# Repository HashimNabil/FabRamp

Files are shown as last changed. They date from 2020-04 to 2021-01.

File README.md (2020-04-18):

# FabRamp

Fabramp is Ramp 1.4 fabable board! its based on Atmega2560 and comes with the following features:
- 6 PWM terminals with STP55NF06L transistors that can be used for multiple Extruders/hot bed/fans
- Extruder Fan terminal
- 2 Extruders terminals with built in Polulu drivers (one of them have terminals for external driver)
- 3 Thermometer terminals with filtering capacitors
- Terminals for 3 axis motors (X, Y and Z)
- Terminals for End stops for all Axis (2 per Axis)
- BLtouch Auto level sensor terminals
- ISP headers
- USB support
- 12V Power terminals with 20A diode as reverse voltage protection
- 5V input with 5A diode as reverse voltage protect

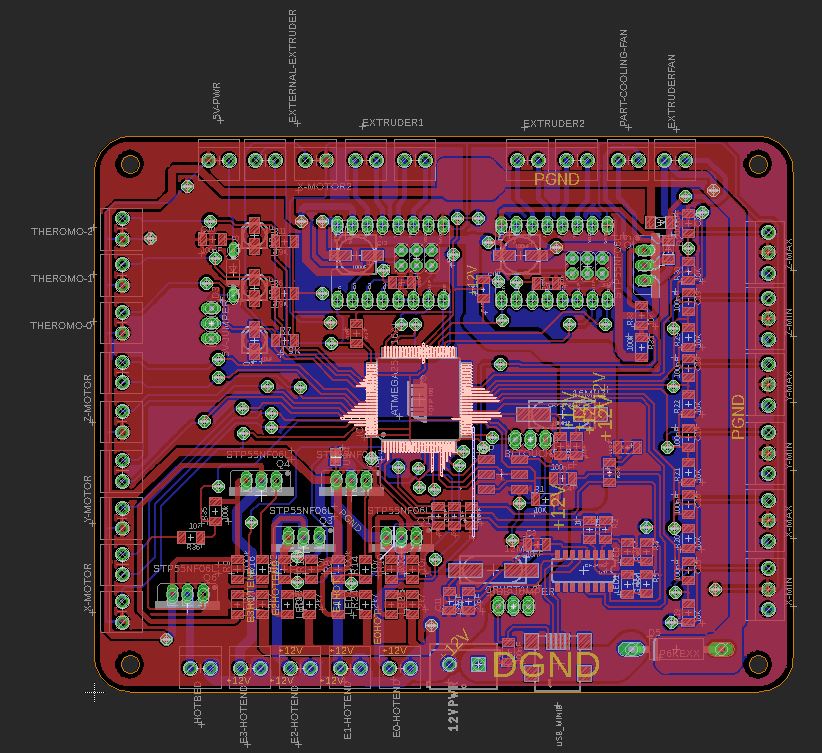
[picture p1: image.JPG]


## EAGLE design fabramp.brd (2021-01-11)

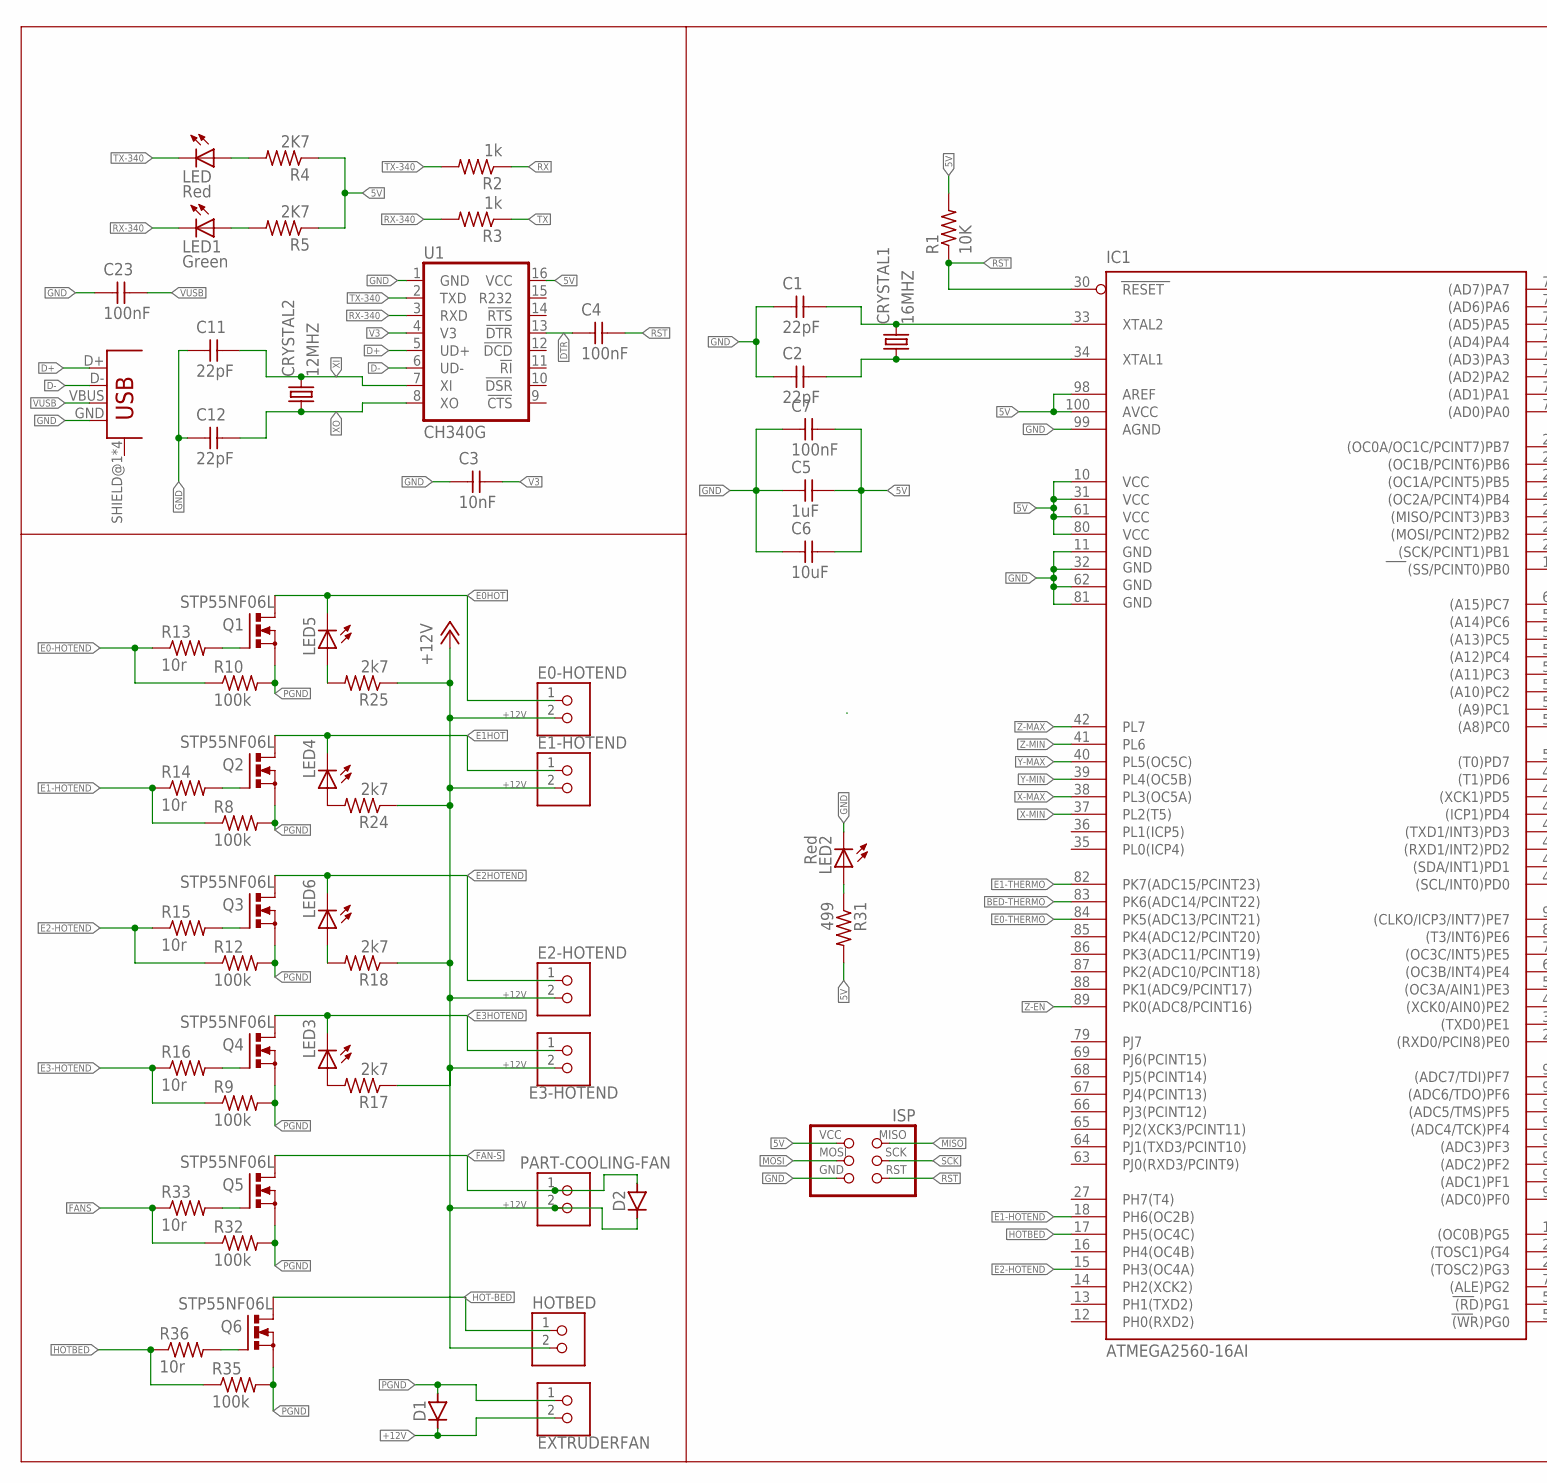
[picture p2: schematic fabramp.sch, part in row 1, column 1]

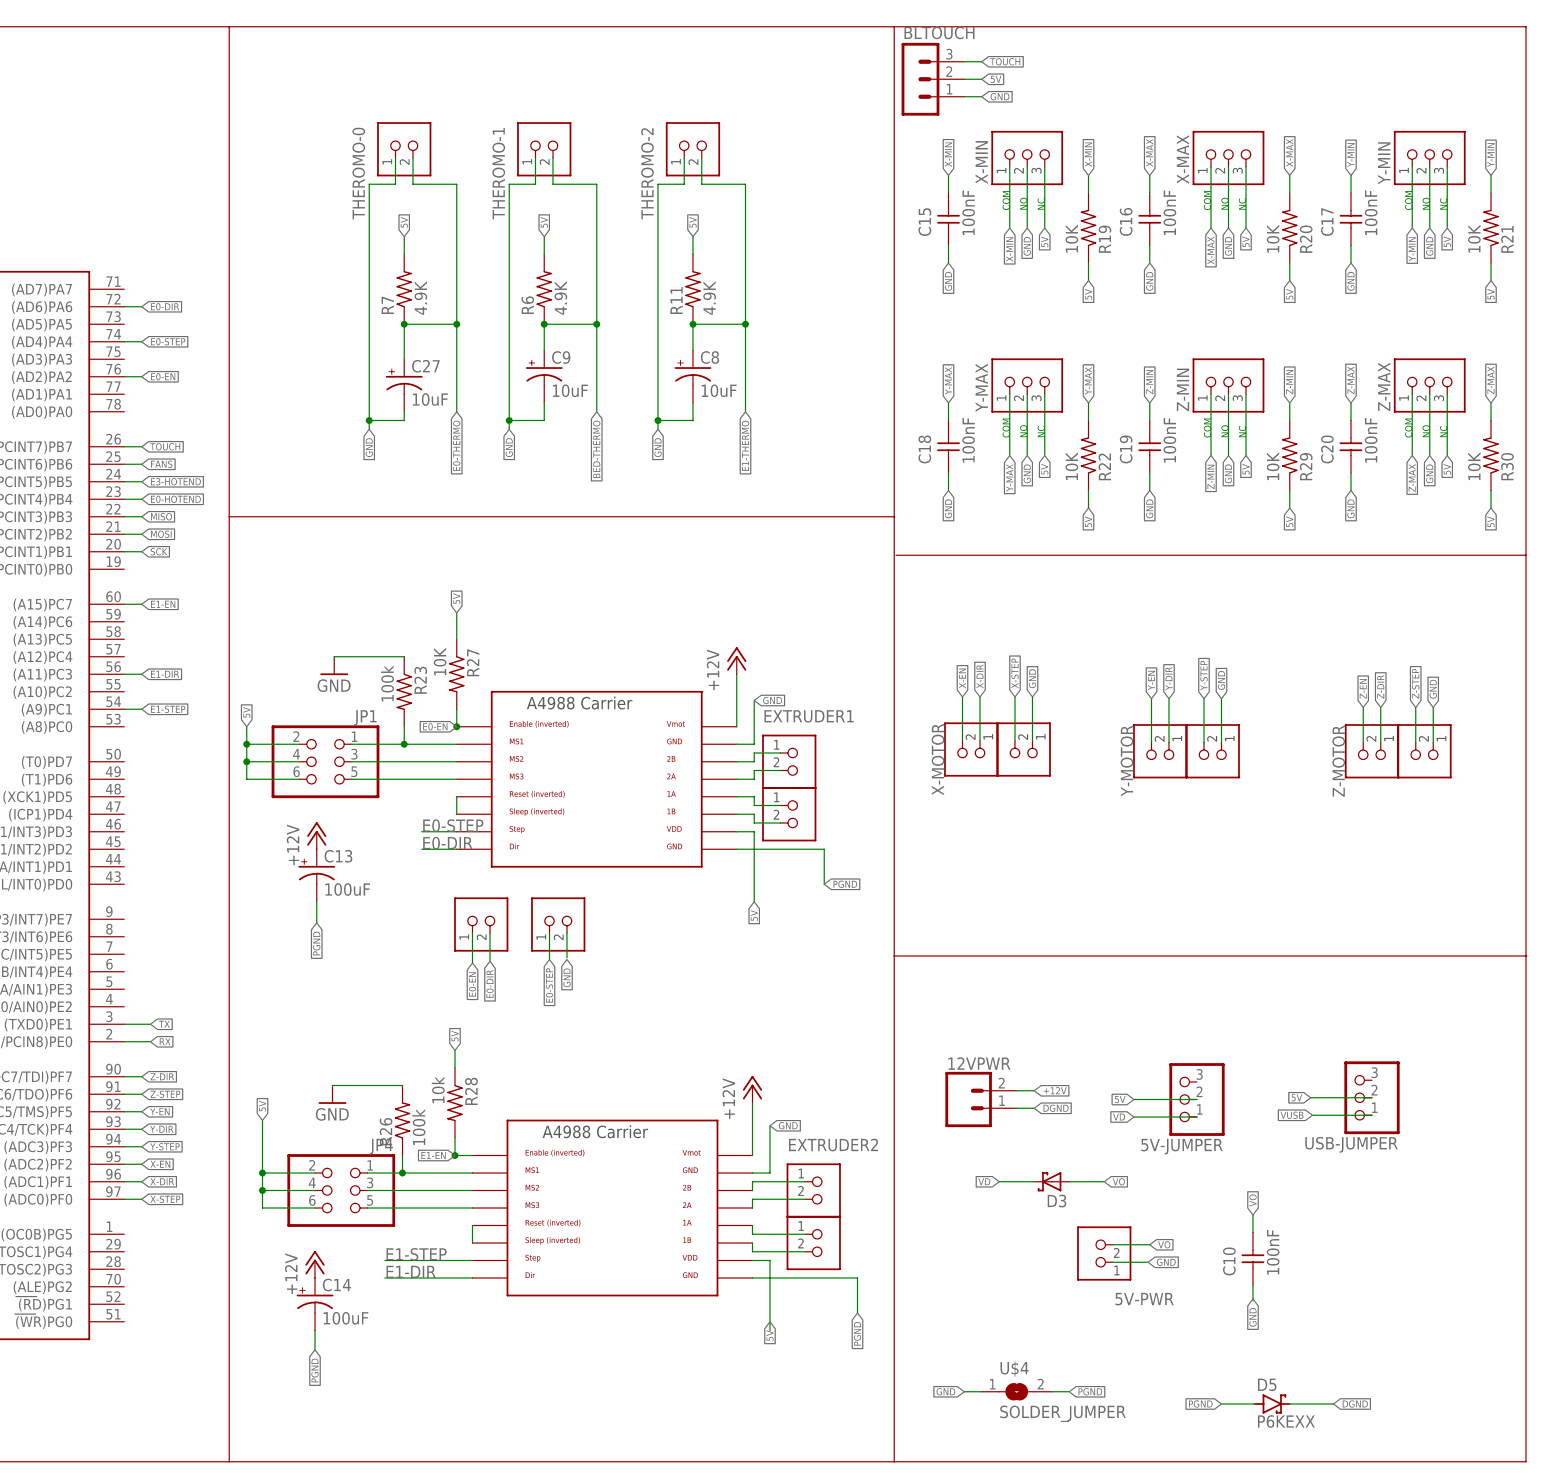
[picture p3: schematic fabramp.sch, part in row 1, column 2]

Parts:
5V-JUMPER: PINHD-1X3; 1X03
5V-PWR: TERM-1X02-FABLAB; ED555DS-2DS
12VPWR: CONN_025MM; SCREWTERMINAL-5MM-2
BLTOUCH: MA03-1
C1, C2, C11, C12: 22pF; C1206FAB
C3: 10nF; C1206FAB
C4, C7, C10, C15, C16, C17, C18, C19, C20, C23: 100nF; C1206FAB
C5: 1uF; C1206FAB
C6: 10uF; C1206FAB
C8, C9, C27: 10uF; 153CLV-0405
C13, C14: 100uF; 153CLV-0605
CRYSTAL1: 16MHZ; CSM-7X-DU
CRYSTAL2: 12MHZ; CSM-7X-DU
D1, D2: CDBM1100-G; MINI-SMA
D3: SCHOTTKY-DIODEDO35-7; DO35-7
D5: P6KEXX; CB417-15
E0-HOTEND, E1-HOTEND, E2-HOTEND, E3-HOTEND: TERM-1X02-FABLAB; ED555DS-2DS
EXTERNAL-EXTRUDER: TERM-1X02-FABLAB; ED555DS-2DS
EXTRUDER1, EXTRUDER2, EXTRUDER11, EXTRUDER22: TERM-1X02-FABLAB; ED555DS-2DS
EXTRUDERFAN: TERM-1X02-FABLAB; ED555DS-2DS
HOTBED: TERM-1X02-FABLAB; ED555DS-2DS
IC1: ATMEGA2560-16AI; TQFP100
ISP: AVRISPSMD; 2X03SMD
JP1, JP4: PINHD-2X3; 2X03
LED, LED2: Red; LED1206FAB
LED1: Green; LED1206FAB
LED3, LED4, LED5, LED6: LEDFAB1206; LED1206FAB
PART-COOLING-FAN: TERM-1X02-FABLAB; ED555DS-2DS
Q1, Q2, Q3, Q4, Q5, Q6: STP55NF06L; TO220BV
R1, R19, R20, R21, R22, R27, R29, R30: 10K; R1206FAB
R2, R3: 1k; R1206FAB
R4, R5: 2K7; R1206FAB
R6, R7, R11: 4.9K; R1206FAB
R8, R9, R10, R12, R23, R26, R32, R35: 100k; R1206FAB
R13, R14, R15, R16, R33, R36: 10r; R1206FAB
R17, R18, R24, R25: 2k7; R1206FAB
R28: 10k; R1206FAB
R31: 499; R1206FAB
THEROMO-0, THEROMO-1, THEROMO-2: TERM-1X02-FABLAB; ED555DS-2DS
U1: CH340G; SO016
U$1: USB_MINIB
U$2, U$3: A4988BREAKOUT
U$4: SOLDER_JUMPER; SJFAB
USB-JUMPER: PINHD-1X3; 1X03
X-MAX: TERM-1X03'-FABLAB'; ED555DS-3DS
X-MIN: TERM-1X03'-FABLAB'; ED555DS-3DS
X-MOTOR, X-MOTOR2: TERM-1X02-FABLAB; ED555DS-2DS
XMOTOR2: TERM-1X02-FABLAB; ED555DS-2DS
Y-MAX: TERM-1X03'-FABLAB'; ED555DS-3DS
Y-MIN: TERM-1X03'-FABLAB'; ED555DS-3DS
Y-MOTOR: TERM-1X02-FABLAB; ED555DS-2DS
YMOTOR2: TERM-1X02-FABLAB; ED555DS-2DS
Z-MAX: TERM-1X03'-FABLAB'; ED555DS-3DS
Z-MIN: TERM-1X03'-FABLAB'; ED555DS-3DS
Z-MOTOR, Z-MOTOR2: TERM-1X02-FABLAB; ED555DS-2DS

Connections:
5V: 5V-JUMPER.2, BLTOUCH.2, C5.2, C6.2, C7.2, IC1.10 (VCC), IC1.31 (VCC1), IC1.61 (VCC2), IC1.80 (VCC3), IC1.98 (AREF), IC1.100 (AVCC), ISP.2 (VCC), JP1.2, JP1.4, JP1.6, JP4.2, JP4.4, JP4.6, R1.2, R4.1, R5.1, R6.2, R7.2, R11.2, R19.1, R20.1, R21.1, R22.1, R27.1, R28.1, R29.1, R30.1, R31.2, U1.16 (VCC), U$2.VDD, U$3.VDD, USB-JUMPER.2, X-MAX.3, X-MIN.3, Y-MAX.3, Y-MIN.3, Z-MAX.3, Z-MIN.3
+12V: 12VPWR.2, C13.+, C14.+, D1.KATHODE, D2.KATHODE, E0-HOTEND.2, E1-HOTEND.2, E2-HOTEND.2, E3-HOTEND.2, EXTRUDERFAN.2, HOTBED.2, PART-COOLING-FAN.2, R17.1, R18.1, R24.1, R25.1, U$2.VMOT, U$3.VMOT
BED-THERMO: C9.+, IC1.83 (PK6(ADC14/PCINT22)), R6.1, THEROMO-1.2
D+: U1.5 (UD+), U$1.D+
D-: U1.6 (UD-), U$1.D-
DGND: 12VPWR.1, D5.C
DTR: C4.1, U1.13 (!DTR)
E0-DIR: EXTERNAL-EXTRUDER.2, IC1.72 ((AD6)PA6), U$2.DIR
E0-EN: EXTERNAL-EXTRUDER.1, IC1.76 ((AD2)PA2), R27.2, U$2.EN
E0-HOTEND: IC1.23 ((OC2A/PCINT4)PB4), R10.1, R13.1
E0-STEP: IC1.74 ((AD4)PA4), U$2.STEP, X-MOTOR2.1
E0-THERMO: C27.+, IC1.84 (PK5(ADC13/PCINT21)), R7.1, THEROMO-0.2
E0HOT: E0-HOTEND.1, LED5.2 (C), Q1.D
E1-DIR: IC1.56 ((A11)PC3), U$3.DIR
E1-EN: IC1.60 ((A15)PC7), R28.2, U$3.EN
E1-HOTEND: IC1.18 (PH6(OC2B)), R8.1, R14.1
E1-STEP: IC1.54 ((A9)PC1), U$3.STEP
E1-THERMO: C8.+, IC1.82 (PK7(ADC15/PCINT23)), R11.1, THEROMO-2.2
E1HOT: E1-HOTEND.1, LED4.2 (C), Q2.D
E2-HOTEND: IC1.15 (PH3(OC4A)), R12.1, R15.1
E2HOTEND: E2-HOTEND.1, LED6.2 (C), Q3.D
E3-HOTEND: IC1.24 ((OC1A/PCINT5)PB5), R9.1, R16.1
E3HOTEND: E3-HOTEND.1, LED3.2 (C), Q4.D
FAN-S: D2.ANODE, PART-COOLING-FAN.1, Q5.D
FANS: IC1.25 ((OC1B/PCINT6)PB6), R32.1, R33.1
GND: 5V-PWR.1, BLTOUCH.1, C1.1, C2.1, C3.1, C5.1, C6.1, C7.1, C8.-, C9.-, C10.1, C11.1, C12.1, C15.1, C16.1, C17.1, C18.1, C19.1, C20.1, C23.1, C27.-, IC1.11 (GND), IC1.32 (GND1), IC1.62 (GND2), IC1.81 (GND3), IC1.99 (AGND), ISP.6 (GND), LED2.2 (C), R23.1, R26.2, THEROMO-0.1, THEROMO-1.1, THEROMO-2.1, U1.1 (GND), U$1.GND, U$2.GND, U$3.GND, U$4.1, X-MAX.2, X-MIN.2, X-MOTOR2.2, XMOTOR2.1, Y-MAX.2, Y-MIN.2, YMOTOR2.1, Z-MAX.2, Z-MIN.2, Z-MOTOR2.1
HOT-BED: HOTBED.1, Q6.D
HOTBED: IC1.17 (PH5(OC4C)), R35.1, R36.1
MISO: IC1.22 ((MISO/PCINT3)PB3), ISP.1 (MISO)
MOSI: IC1.21 ((MOSI/PCINT2)PB2), ISP.4 (MOSI)
unnamed: C1.2, CRYSTAL1.2, IC1.33 (XTAL2)
unnamed: C2.2, CRYSTAL1.1, IC1.34 (XTAL1)
unnamed: LED2.1 (A), R31.1
unnamed: EXTRUDER22.1, U$3.2B
unnamed: EXTRUDER22.2, U$3.2A
unnamed: EXTRUDER2.1, U$3.1A
unnamed: LED.1 (A), R4.2
unnamed: LED1.1 (A), R5.2
unnamed: EXTRUDER2.2, U$3.1B
unnamed: Q5.G, R33.2
unnamed: Q4.G, R16.2
unnamed: Q3.G, R15.2
unnamed: LED3.1 (A), R17.2
unnamed: LED6.1 (A), R18.2
unnamed: Q6.G, R36.2
unnamed: JP1.5, U$2.MS3
unnamed: U$2.RST, U$2.SLP (SLEEP)
unnamed: U$3.RST, U$3.SLP (SLEEP)
unnamed: JP4.1, R26.1, U$3.MS1
unnamed: JP1.1, R23.2, U$2.MS1
unnamed: JP1.3, U$2.MS2
unnamed: JP4.5, U$3.MS3
unnamed: JP4.3, U$3.MS2
unnamed: EXTRUDER11.1, U$2.2B
unnamed: EXTRUDER11.2, U$2.2A
unnamed: EXTRUDER1.1, U$2.1A
unnamed: EXTRUDER1.2, U$2.1B
unnamed: LED4.1 (A), R24.2
unnamed: Q2.G, R14.2
unnamed: Q1.G, R13.2
unnamed: LED5.1 (A), R25.2
PGND: C13.-, C14.-, D1.ANODE, D5.A, EXTRUDERFAN.1, Q1.S, Q2.S, Q3.S, Q4.S, Q5.S, Q6.S, R8.2, R9.2, R10.2, R12.2, R32.2, R35.2, U$2.GND@0 (GND), U$3.GND@0 (GND), U$4.2
RST: C4.2, IC1.30 (RESET), ISP.5 (RST), R1.1
RX: IC1.2 ((RXD0/PCIN8)PE0), R2.1
RX-340: LED1.2 (C), R3.2, U1.3 (RXD)
SCK: IC1.20 ((SCK/PCINT1)PB1), ISP.3 (SCK)
TOUCH: BLTOUCH.3, IC1.26 ((OC0A/OC1C/PCINT7)PB7)
TX: IC1.3 ((TXD0)PE1), R3.1
TX-340: LED.2 (C), R2.2, U1.2 (TXD)
V3: C3.2, U1.4 (V3)
VD: 5V-JUMPER.1, D3.C
VO: 5V-PWR.2, C10.2, D3.A
VUSB: C23.2, U$1.VBUS, USB-JUMPER.1
X-DIR: IC1.96 ((ADC1)PF1), X-MOTOR.1
X-EN: IC1.95 ((ADC2)PF2), X-MOTOR.2
X-MAX: C16.2, IC1.38 (PL3(OC5A)), R20.2, X-MAX.1
X-MIN: C15.2, IC1.37 (PL2(T5)), R19.2, X-MIN.1
X-STEP: IC1.97 ((ADC0)PF0), XMOTOR2.2
XI: C11.2, CRYSTAL2.2, U1.7 (XI)
XO: C12.2, CRYSTAL2.1, U1.8 (XO)
Y-DIR: IC1.93 ((ADC4/TCK)PF4), Y-MOTOR.1
Y-EN: IC1.92 ((ADC5/TMS)PF5), Y-MOTOR.2
Y-MAX: C18.2, IC1.40 (PL5(OC5C)), R22.2, Y-MAX.1
Y-MIN: C17.2, IC1.39 (PL4(OC5B)), R21.2, Y-MIN.1
Y-STEP: IC1.94 ((ADC3)PF3), YMOTOR2.2
Z-DIR: IC1.90 ((ADC7/TDI)PF7), Z-MOTOR.1
Z-EN: IC1.89 (PK0(ADC8/PCINT16)), Z-MOTOR.2
Z-MAX: C20.2, IC1.42 (PL7), R30.2, Z-MAX.1
Z-MIN: C19.2, IC1.41 (PL6), R29.2, Z-MIN.1
Z-STEP: IC1.91 ((ADC6/TDO)PF6), Z-MOTOR2.2

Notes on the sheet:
COM

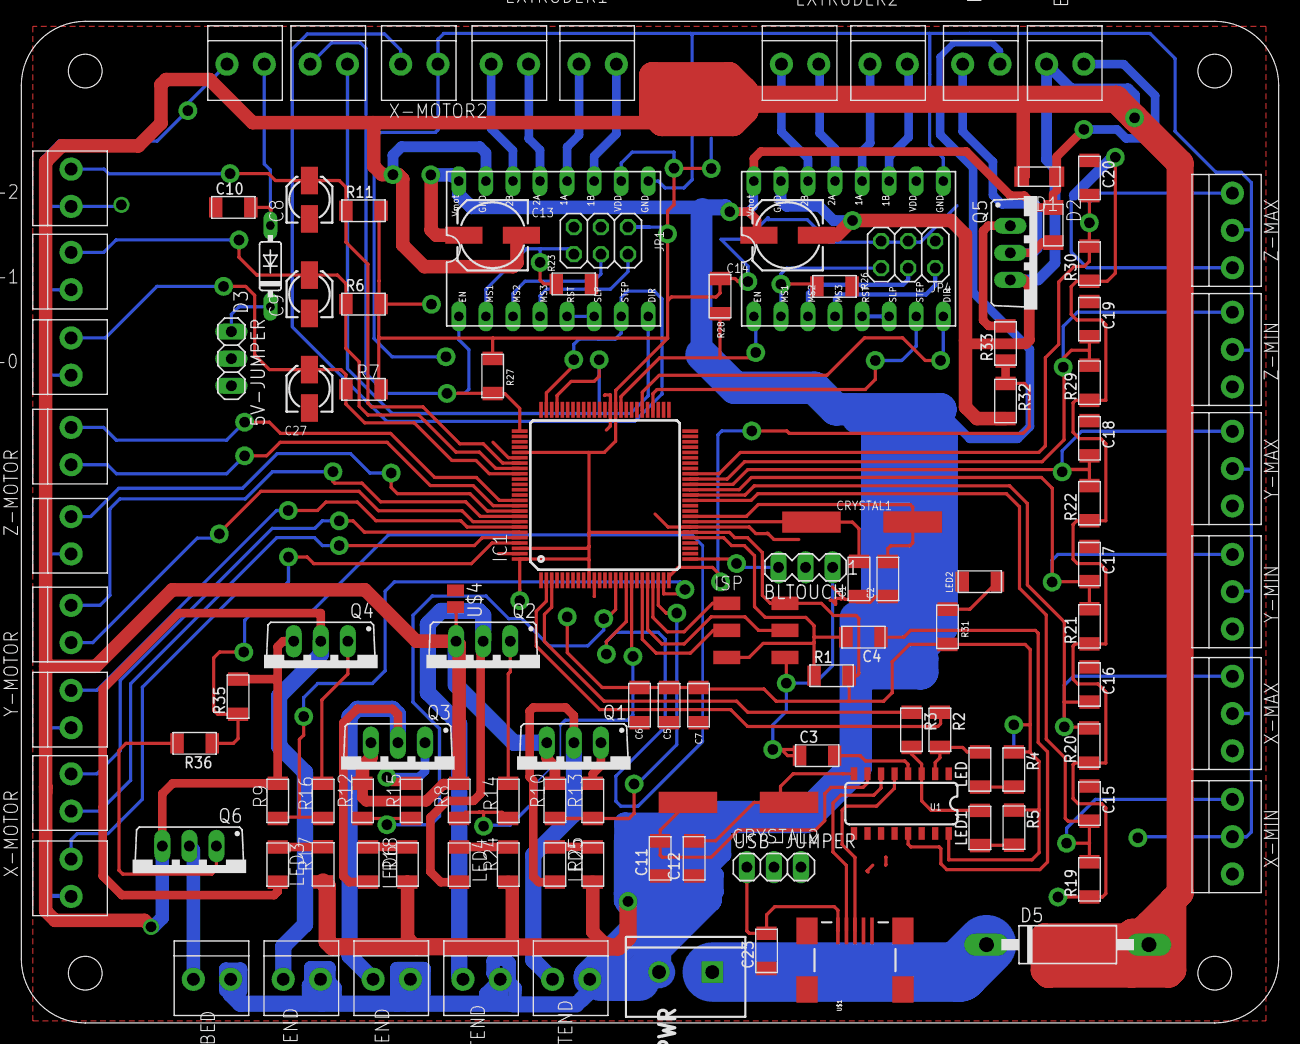
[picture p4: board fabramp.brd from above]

Board: 2 copper layers, 118.0 x 94.0 mm, 118 parts (0 on the bottom side), 90 nets.

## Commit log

2020-04-18 first commoit
    [bigmaker.brd, bigmaker.sch]
2021-01-11 added holes
    [fabramp.brd, fabramp.sch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]

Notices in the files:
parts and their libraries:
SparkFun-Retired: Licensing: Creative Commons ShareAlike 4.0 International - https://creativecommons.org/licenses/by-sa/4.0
